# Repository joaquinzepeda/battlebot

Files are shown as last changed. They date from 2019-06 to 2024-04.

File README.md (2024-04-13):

# Rotorcraft - 2019
Battle-bot que consiste en una hélice que lo recubrirá, la cual será su arma y su defensa. Y se moverá con 2 ruedas traseras y una rueda delantera con su eje libre.

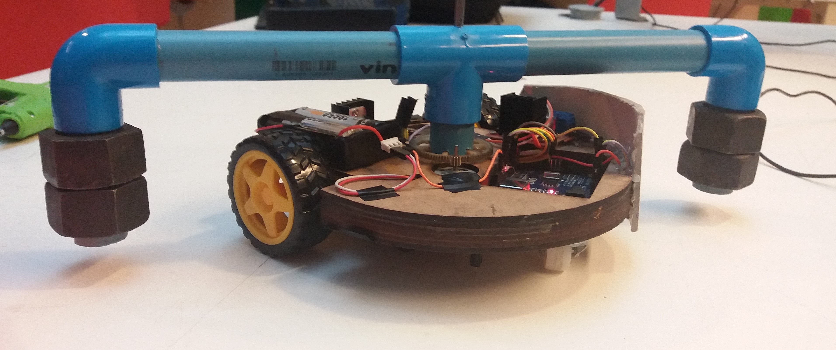
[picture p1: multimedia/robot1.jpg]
Robot "Rotor-Craft"


## Integrantes
Alejandro Chepillo - Fcfm
Raimundo Andrade - Fcfm
Joaquín Zepeda - Fcfm

## Descripción del proyecto

Nuestro Robot tiene una base redondeada de madera en donde se encuentra el arduino y los circuitos utilizados, consta de 3 ruedas. 2 Ruedas traseras impulsadas por motores DC y una rueda delantera centrada con un eje libre para moverse con libertad. En el centro de la base se encuentra un eje, este eje mediante unos engranajes se une a un motor brushless de dron reciclado. En la parte superior se encuentra una unión en forma de "T", perpendicular a este eje y a través de la unión pasa un tubo de PVC que se curva en 90 grados acercándose al final de cada extremo, lo suficiente como para que cubra el robot al girar este eje. En ambos extremos se encuentran unidas unas tuercas sólidas.

### Estrategia utilizada

Nuestra estrategia consistió en crear un robot en el cual su mecanismo de defensa y ataque sean el mismo, de forma que si nos tratan de atacar, el agresor sufriría un daño colateral como efecto de atacar a nuestro robot.

#### Ofensiva y Defensiva

El eje que está unido a unos tubos PVC en la parte superior giraría por acción de un motor brushless produciendo que el tubo PVC perpendicular gire con mucha velocidad, y debido a que este tubo cuenta de caída con unas tuercas en los extremos de esta forma acercándose a los robots enemigos, los golpearía y no sufriría daño, ya que al girar en torno a la base circular la protegería también, funcionando esta arma como un mecanismo de defensa y ataque.

### Descripción de la aplicación.

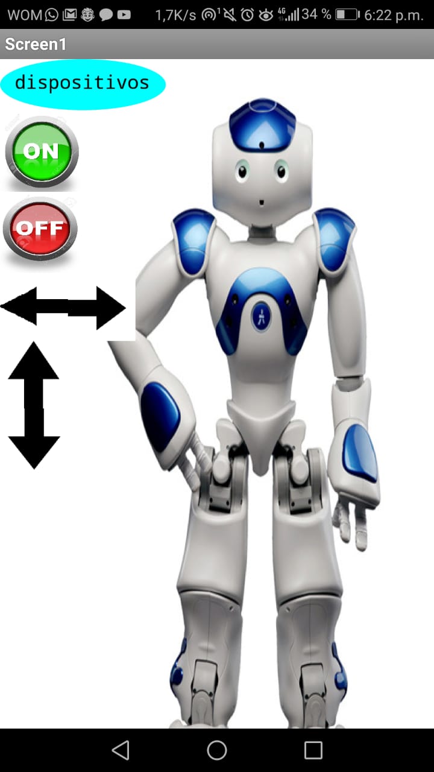
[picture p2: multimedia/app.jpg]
aplicación


La aplicación hecha en MIT Inventor para controlar nuestro battle bot consta de 7 botones. 2 botones para que se mueva adelante y atrás haciendo girar las ruedas a la misma revolución y para que avancen en el mismo sentido, otros 2 botones para que gire en sí mismo a la derecha o a la izquierda, producto de que ambas ruedas se muevan a las mismas revoluciones, pero con sentido de giro contrario. Otro par de botones tenían la función de encender y apagar el arma a distancia, sin embargo, este sistema no se utilizó al final, debido a que el puente H utilizado no dejaba pasar el suficiente amperaje, quitándole rendimiento a nuestra arma, por lo que esta función se reemplazó por un interruptor manual. Finalmente, el último botón tiene la finalidad de abrir una pantalla en la cual aparecen los posible dispositivos a los que conectarse mediante bluetooth.

### Diagrama funcional

<Diagrama general de funcionamiento. Se sugiere un esquema de sistemas, completo.>

### *BONUS*: Paso a Paso

paso 1: estar motivados para crear una máquina de matar.

paso 2: comprar y/o reciclar materiales, los cuales son: - 50 cm de tubo de PVC de 25 mm - pegamento para PVC (vinilit) - dos codos y una T para el tubo de PVC - 4 tuercas de una pulgada - un pedazo de madero 30x30x3 cm - un motor de helicóptero o alguno similar, con un controlador para este. - 2 motores DC con ... - un puente H L298n - 2 ruedas con tracción - 1 rueda pivote - una gran cantidad de cables con conexiones macho-macho, macho-hembra - 4 pilas 18650 - 2 porta pilas - bluetooth HC06 - Arduino uno - un interruptor con gran capacidad ... - 4 cables gruesos - silicona - cola fría para madera *una cortadora láser - prensa - un eje de metal de al menos 15 cm de altura - cinta aislante - un engranaje o mecanismo para conectar el eje con el motor * decoración a gusto *materiales opcionales

paso 3: lo primero que haremos, será construir la base para nuestro battlebot, para esto cortaremos la madera con nuestros planos, de preferencia con una cortadora láser, pero también puede utilizar otros métodos, los cortes del borde no necesitan ser tan precisos, pero el corte redondo (para el motor) debe ser lo más preciso posible, (el tamaño de este orificio puede variar dependiendo del porte del motor que tengan) ahora tienen que pegar todas las capas, menos la que va más arriba, para esto usaremos la cola fría, y después pondremos la base en la prensa para que queden bien pegadas las capas.

paso 4: conectar el circuito, para probar que funcione todo sin problemas, después de que ya funcione todo bien por separado, colocar el Arduino y el puente H en sus posiciones correctas, y pasar los cables correspondientes por los caminos de la madera (puente H-hacia las ruedas puente H-hacia las pilas, puente H-Arduino)

paso 5: pegar la capa de arriba de la madera.

Paso 6: conectar las ruedas con los motores DC, y pegar la rueda pivote.

Paso 7: ensamblar las demás cosas, conectando las cosas en sus respectivos pines y preocupándose de que los cables no sobresalgan mucho y que los componentes no estén muy cerca del engranaje para que no molesten el funcionamiento de este, colocar el engranaje, el motor y el eje.

Paso 8: ahora armemos el arma, cortar el tubo para tener 2 tubos de 7 cm, 1 tubo de 3 cm, 2 tubos de 14 cm, conectarlos (pegándolos con pegamento para PVC, tengan cuidado, infórmense de cómo pegarlo bien chicos) para formar una M, con los de 7 cm en los extremos y el de 3 cm en el centro. Después hacer un orificio en el centro de la T para atravesar el eje (que quede bastante preciso, para que se pueda afirmar bien)

Paso 9: pegar el eje (según su forma de conectar el motor con el eje) al engranaje, y el eje pegarlo a la base, dejando un libre movimiento para el engranaje (traten de hacerlo lo más simétrico posible, y el eje lo más vertical, para que no sufra otros movimientos. Preocuparse de encajar bien el motor con el engranaje, hacer pruebas para ver que gire sin problemas.

Paso 10: conectar el motor a las pilas, y asegurarse de que todos los componentes estén bien fijos en su posición (no queremos problemas futuros)

Paso 11: colocar las tuercas en los extremos del tubo de 7 cm, asegurándose que queden bien fijas (si es necesario, ponerle algún tipo de pegamento)

Paso 12: colocar su battlebot en el piso, conectarlo con la aplicación, prender el arma y disfrutar de destruir a tus oponentes.

### Problemas y soluciones

Primero tuvimos que descifrar cómo sería la base correcta para crear nuestro robot, ya que teóricamente ya lo teníamos pensado. Lo siguiente fue que ya al obtener unos motores reciclados para nuestra arma, estos al conectarlos a unas pilas comunes no funcionaban, y nos dimos cuenta que necesitaban unas pilas con mayor amperaje, por lo que conseguimos unas pilas adecuadas y sus complementos para conectarlas adecuadamente. Finalmente otro problema que surgió, fue que queríamos poder encender y apagar el arma a distancia, por lo que nos conseguimos un puente H igual al usado para las ruedas traseras para poder asignarlo a un pin y así manejarlo. Sin embargo, este puente no dejaba pasar suficiente corriente por lo que se calentaba mucho, y el arma no funcionaba adecuadamente, por lo que decidimos al final cambiar este sistema por un interruptor manual.

### Proyecciones a futuro

A futuro hemos pensado en mejoras, como cambiar el interruptor manual por uno digital de forma que lo controlemos a distancia. Agregarle más peso y espacio a la base central de nuestro robot para que todo esté mejor acomodado y sea más estable. Y hemos pensado en aumentar el peso o la densidad del arma (hélice), para que sea más resistente al momento de golpear un objeto duro, de manera que resista sin problemas.

También creemos que nuestro battlebot tiene mucho potencial en el mismo ámbito de peleas, ya que no consta de mecanismos muy complicados por lo que se le podrían agregar diferentes funciones para hacerlo más peligroso. También podría ser útil como un robot de limpieza si en los extremos del arma se intercambiaran las tuercas, por escobillas, podría ser bastante eficiente a la hora de barrer o trapear.]

## UPDATE 

Participamos en la Beauchef robotics challenge (BRC) con una versión mejorada la cual cambiaba el PVC por tubos de metal. 

## Licencia
<br />Esta obra está bajo una <a rel="license" href="http://creativecommons.org/licenses/by-nc/4.0/">Licencia Creative Commons Atribución-NoComercial 4.0 Internacional</a>.

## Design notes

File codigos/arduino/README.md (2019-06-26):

# Códigos Arduino

Subir códigos **comentados** utilizados en Arduino.

ROTORCRART

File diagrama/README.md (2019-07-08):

# Diagrama electromecánico

Diagrama electromecánico realizado en [Fritzing](http://fritzing.org/home/)

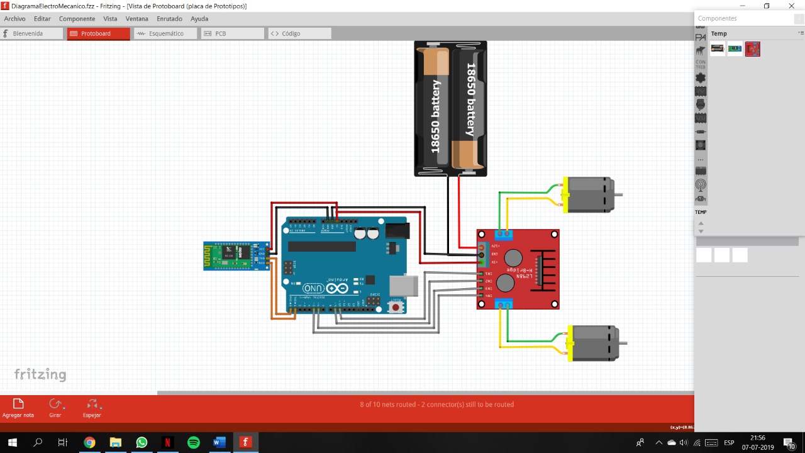
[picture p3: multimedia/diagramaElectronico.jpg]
Diagrama Electronico


### Diagrama de flujo

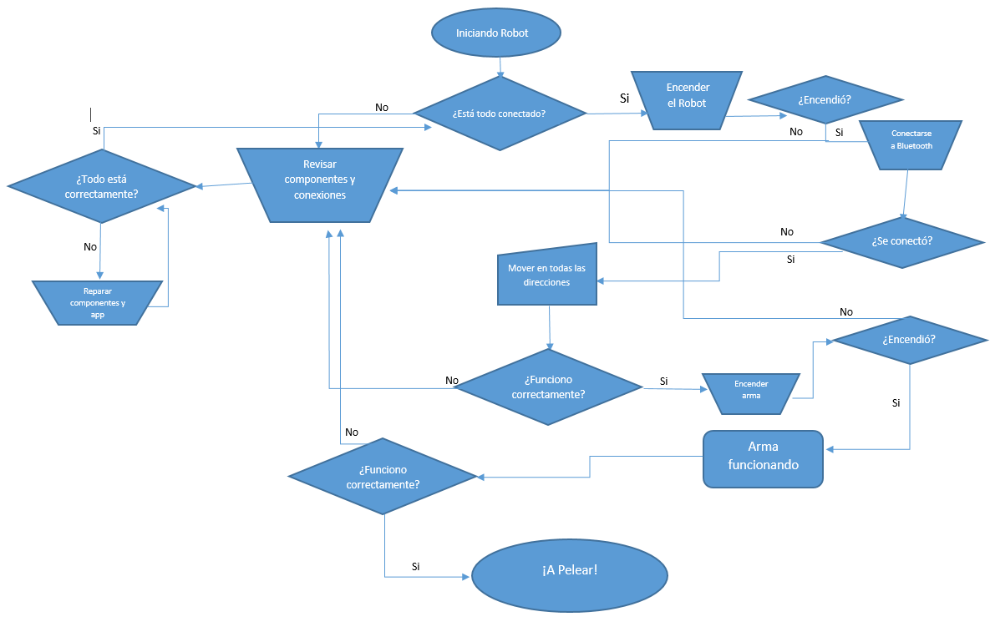
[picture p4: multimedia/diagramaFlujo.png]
Diagrama de Flujo


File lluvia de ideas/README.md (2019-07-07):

# Lluvia de Ideas

Subir imágenes y/o vídeos que les sirvieron como búsqueda/inspiración externa.
Subir bocetos, con una breve expicación de las ideas del boceto.

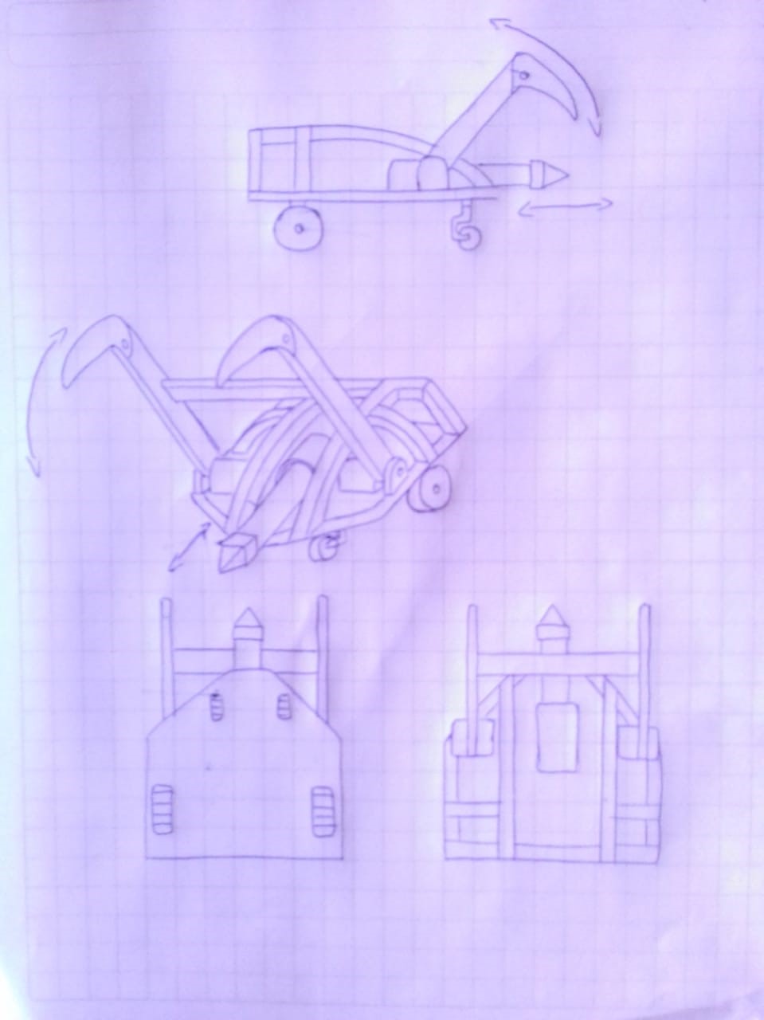
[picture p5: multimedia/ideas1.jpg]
Lluvia de ideas


Un movil que agarraria al enemgo y con un arma punzante atacaria al enemigo en la parte frontal.

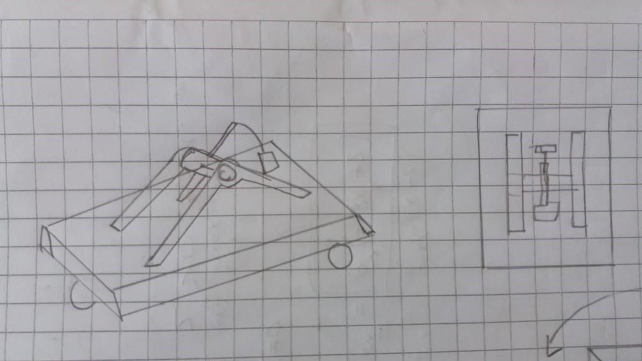
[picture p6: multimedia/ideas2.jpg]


Un movil que se moveria y atacaria con un mecanismo similar a una catapulta en la parte superior.

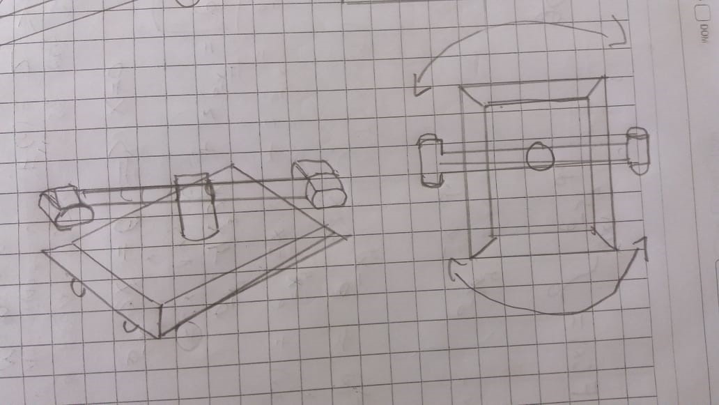
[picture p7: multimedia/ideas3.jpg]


Un movil que consta con un ejey un arma perpendicular que giraria y golpearia a los enemigos.

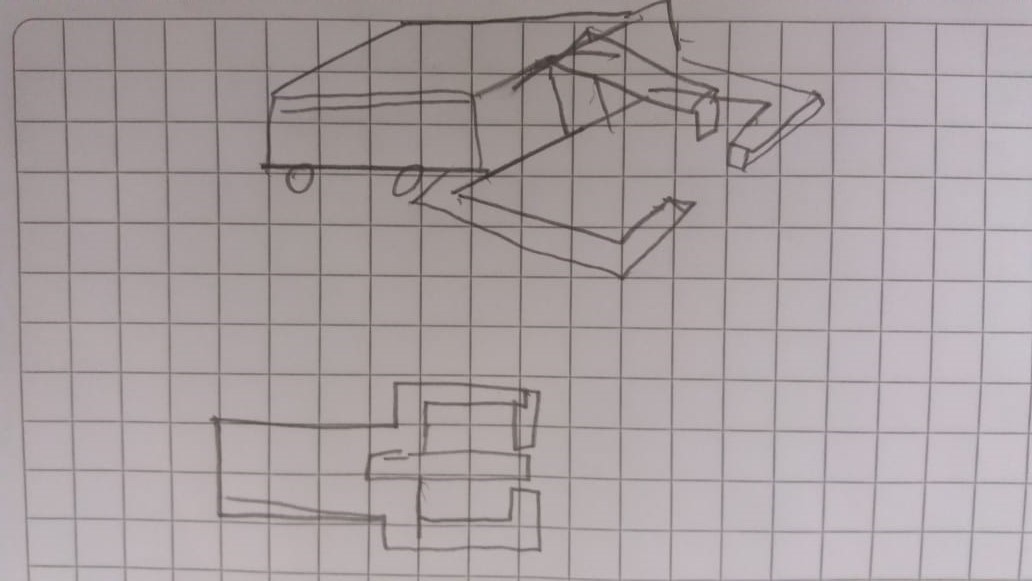
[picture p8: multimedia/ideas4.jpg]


Un movil que agarraria al enemigo y lo aplastaria con unos brazos.

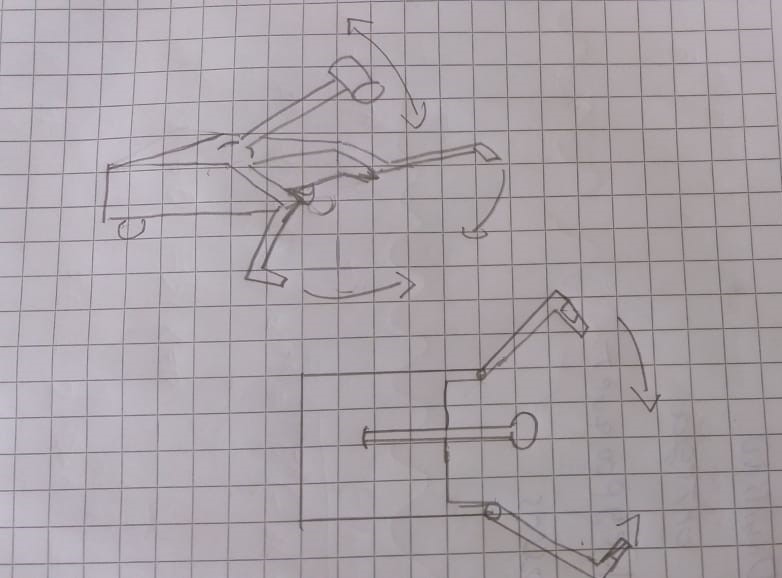
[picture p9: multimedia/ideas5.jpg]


Un movil que agarraria al enemigo y lo golpearia en su parte superior con un martillo.

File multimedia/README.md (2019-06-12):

# Archivos multimedia de los battlebots

Se deben subir:
- Fotos de avance (en orden cronológico)
- Foto del proyecto terminado
- Vídeo de demostración/funcionamiento

Se sugiere subir todas las imágenes y vídeos a esta carpeta y linkearlos desde acá para otros archivos.

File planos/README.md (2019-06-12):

# Archivos de planos incluidos

Subir al repositorio todos los modelos y planos utilizados para construir el battlebot:

- Modelo 3D
- Planos de corte de cortadora láser (.pdf)

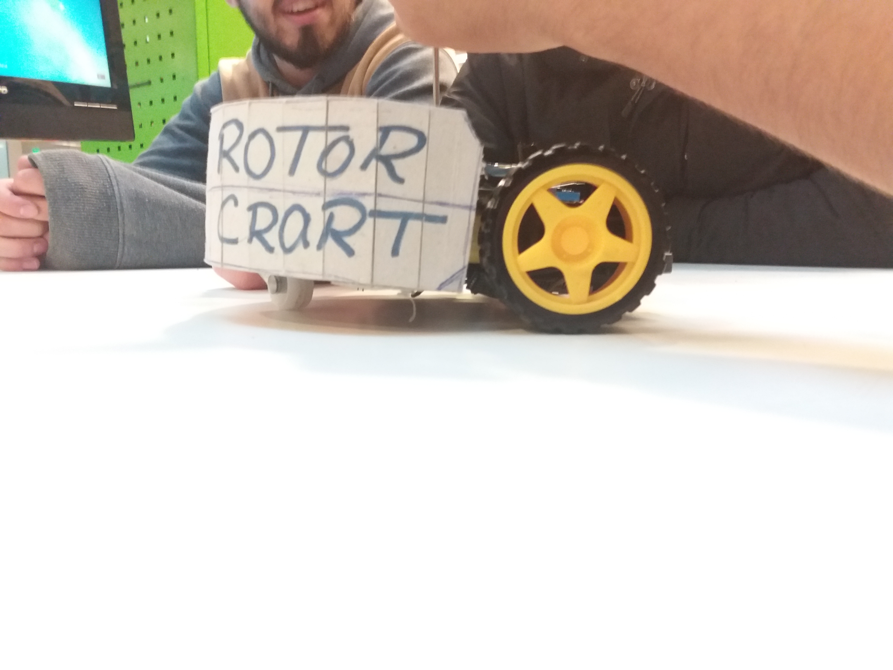
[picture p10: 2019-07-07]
multimedia/robot3.jpg

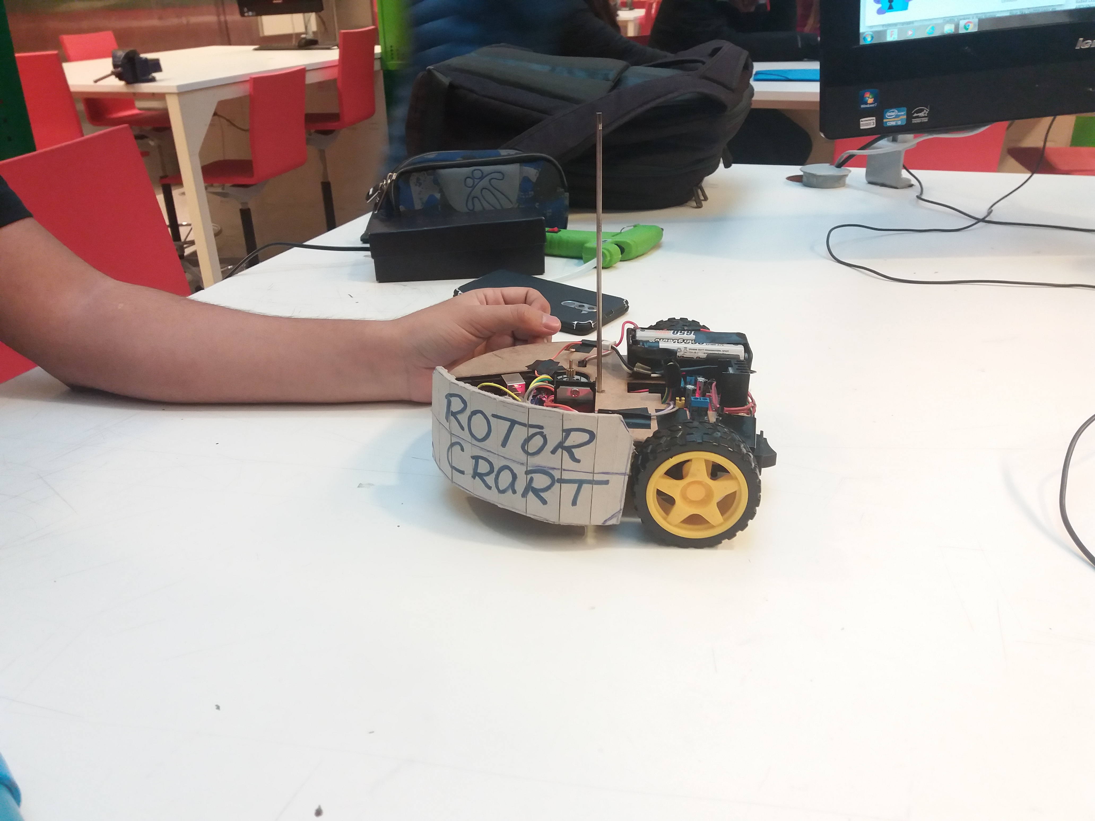
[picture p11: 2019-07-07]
multimedia/robot6.jpg

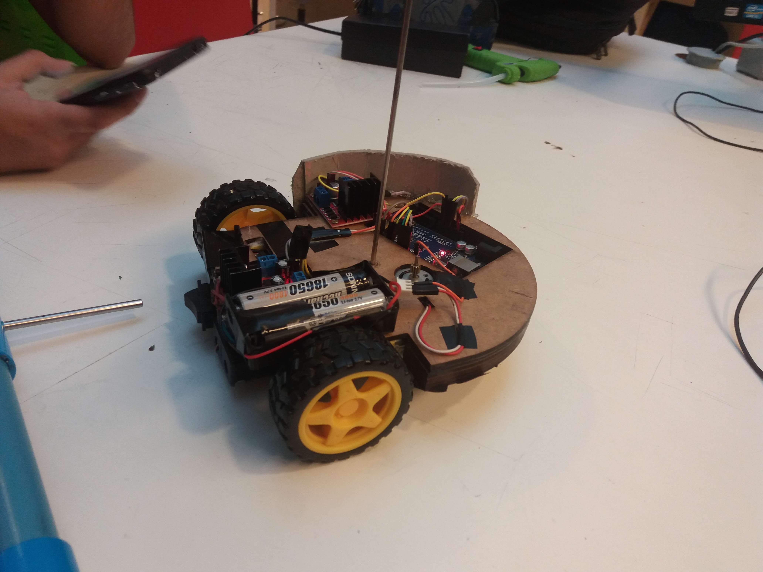
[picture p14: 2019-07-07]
multimedia/robot5.jpg

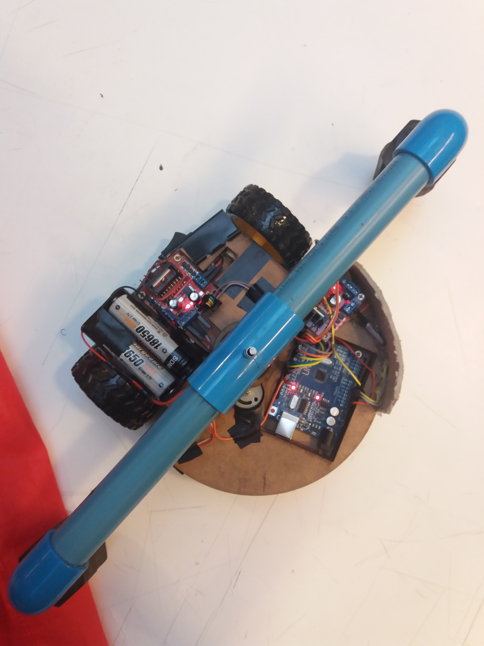
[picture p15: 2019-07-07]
multimedia/robot2.jpg

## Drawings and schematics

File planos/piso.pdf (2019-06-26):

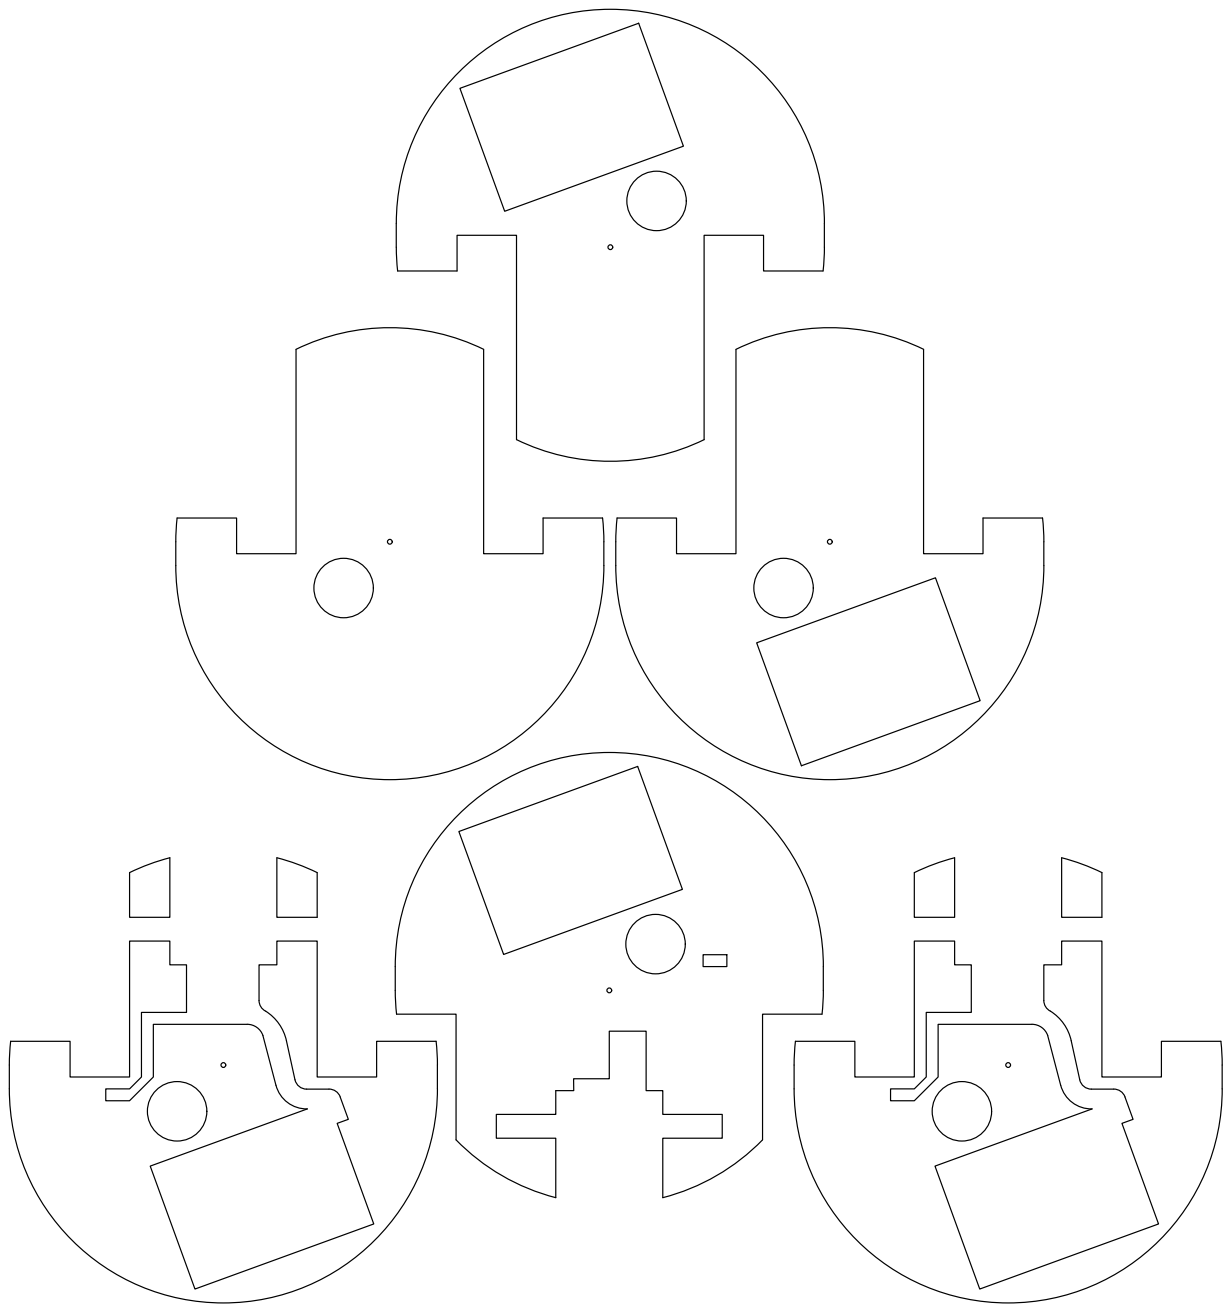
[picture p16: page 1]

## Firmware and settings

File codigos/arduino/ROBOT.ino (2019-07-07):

//Alfa Bots


int motorAanthor = 5; 
int motorAhor = 6; 
int motorBanthor = 9; 
int motorBhor = 10; 
int armaA = 3;
int armaB = 12;

/*
 Variables establecidas para controlar el robot y sus armas
 */
  
  

void setup()  { 
  pinMode(motorBhor, OUTPUT);
  pinMode(motorBanthor, OUTPUT);
  pinMode(motorAhor, OUTPUT);
  pinMode(motorAanthor, OUTPUT);
  pinMode(armaA, OUTPUT);
  pinMode(armaB,OUTPUT);
  Serial.begin(9600);
 } 

 /*
  Pines asignados para cumplir con las funciones requeridas por las variables.
  */
 
void loop()  
{
  
  
  
  
  
  
  
  if(Serial.available() >0)/* detecta si se envian señales y se interpretan a continuacion, la funciones disponibles son mover hacia adelante, atras, izquierda, derecha y accionar el arma. */
  {
    Serial.print("RECEIVED ");
    
    char entrada=Serial.read();
    Serial.print(entrada);
    Serial.print(" ");
    
    if(entrada=='F')
    {
      digitalWrite(motorBhor,LOW);
      digitalWrite(motorBanthor,LOW);
      digitalWrite(motorAhor,LOW);
      digitalWrite(motorAanthor,LOW);
    }      

    if(entrada=='O')
    {
      digitalWrite(armaA,HIGH);
      digitalWrite(motorBanthor,LOW);
    }

     if(entrada=='G')
    {
      digitalWrite(armaA,LOW);
      digitalWrite(motorBanthor,LOW);
    }
  
  
    
    
    if (entrada=='U')
    {
      digitalWrite(motorAhor,HIGH);
      digitalWrite(motorBhor,HIGH);
      digitalWrite(motorBanthor,LOW);
      digitalWrite(motorAanthor,LOW);
      
    
    
      
      if(Serial.available() >0) 
        {
        entrada=Serial.read();
      
      }
    }
    if (entrada=='D')
    {
      digitalWrite(motorAanthor,HIGH);
      digitalWrite(motorBanthor,HIGH);
      digitalWrite(motorAhor,LOW);
      digitalWrite(motorBhor,LOW);
    
    
      
      if(Serial.available() >0) 
        {
          entrada=Serial.read();
        
      }
    
    }
    if (entrada=='L')
    {  //izquierda
    
      digitalWrite(motorAhor, HIGH);
      digitalWrite(motorBanthor, HIGH);
      digitalWrite(motorAanthor,LOW);
      digitalWrite(motorBhor,LOW);
    
      
      if(Serial.available() >0) {
        entrada=Serial.read();
        
        }
    
      }
    if (entrada=='R'){  //derecha
    
      digitalWrite(motorAanthor,HIGH);
      digitalWrite(motorBhor,HIGH);
      digitalWrite(motorAhor, LOW);
      digitalWrite(motorBanthor, LOW);
    
    
      
      if(Serial.available() >0) {
        entrada=Serial.read();
        
        }
    
      }
  }
  
  
  
    
}

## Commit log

2019-06-26 incluyendo nombres de integrantes
2019-07-01 agregar diagrama electromecanico
    [DiagramaElectroMecanico.fzz]
2019-07-07 Codigo en arduino comentado
2019-07-07 Avance en el archivo README.md
2019-07-07 Imagenes agregadas a la multimedia
2019-07-07 Editando lluvia de ideas
2019-07-07 completando lluvia de ideas
2019-07-08 añadiendo diagrama de flujo
2019-07-08 añadiendo relacion en readme con el diagrama electronico
